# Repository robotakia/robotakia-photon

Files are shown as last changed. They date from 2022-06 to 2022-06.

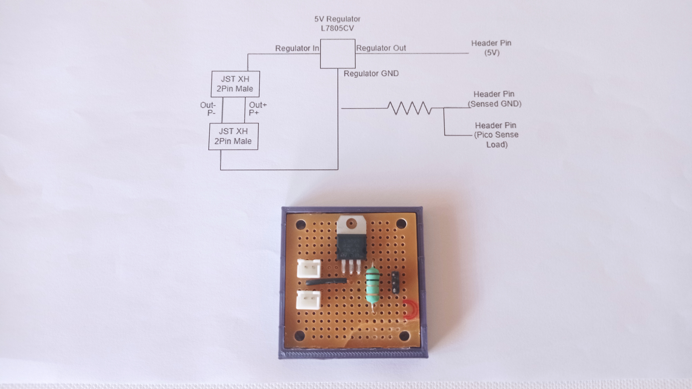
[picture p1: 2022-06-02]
Hardware/Examples/voltage regulator.jpg

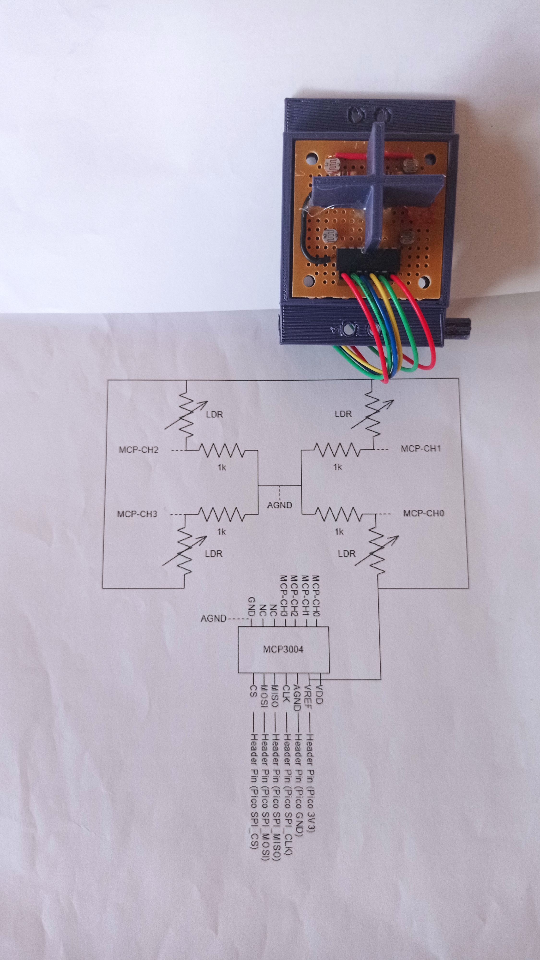
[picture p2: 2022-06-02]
Hardware/Examples/sun tracking sensors.jpg

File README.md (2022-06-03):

# robotakia-photon

Καθώς η ηλεκτρική ενέργεια αποτελεί ένα απαραίτητο αγαθό στον σημερινό τρόπο ζωής μας, σκεφτήκαμε να υλοποιήσουμε ένα σύστημα παραγωγής πράσινης ενέργειας. Η υλοποίηση βασίζεται στην τεχνολογία των φωτοβολταϊκών κυψελών και το σύστημα θα σχεδιαστεί με τρόπο που να μεγιστοποιεί την παραγωγή ενέργειας από τον ήλιο καθ’ όλη τη διάρκεια της μέρας.

-	Η συστοιχία των φωτοβολταϊκών κυψελών θα έχει δύο βαθμούς ελευθερίας, δύο κινητήρες ελέγχουν τον προσανατολισμό του συστήματος
-	Θα υλοποιηθεί πλακέτα/αισθητήρας για αναγνώριση της θέσης του ήλιου, η πλακέτα θα αποτελείται από φωτοαντιστάτες τους οποίους θα «διαβάζει» ο μικροεπεξεργαστής (raspberry pi pico)
-	Το σύστημα θα κάνει αυτόματες διορθώσεις προσανατολισμού πάνω/κάτω και δεξιά/αριστερά για να μεγιστοποιείται η παραγωγή ηλεκτρικής ενέργειας κατά τη διάρκεια της μέρας, ο ιδανικός προσανατολισμός θα προκύπτει από τις τιμές των φωτοαντιστάσεων

Η σελίδα του διαγωνισμού είναι https://openedtech.ellak.gr/robotics2022/sun-tracking-solar-panel-robotakia-photon/

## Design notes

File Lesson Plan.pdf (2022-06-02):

## Περιεχόμενα

## Προετοιμασία

### Λογισμικό

Thonny: Για την συγγραφή του κώδικα Python για το Raspberry Pi Pico.

Tinkercad: Για την σχεδίαση των δομικών στοιχείων.

Prusa Slicer: Για την δημιουργία του gcode για τον 3D εκτυπωτή.

### Εξοπλισμός

Απαραίτητος εξοπλισμός:

- Σταθμός συγκόλλησης
- 3D εκτυπωτής

Βοηθητικός εξοπλισμός:

- Θερμόκολλα

### Υλικά

Quantity | Description
1 | Li-ion Battery Charger Protection Module 2S 3A
1 | Μετατροπέας DC-DC Step-Up 5-35V 2A
2 | Μπαταριοθήκη 1x18650 - με Καλώδια
2 | Μπαταρία Λιθίου 18650 3.7V
1 | Raspberry Pi Pico
2 | Pin Header 1x40 Male 2.54 mm Black
1 | Voltage Regulator L7805CV - 5V 1.5A
2 | Servo Micro 1.8kg.cm Metal Gears (Feetech FS90MG)
4 | Φωτοαντίσταση LDR 5mm
2 | Πλακέτα Διάτρητη 91x45mm (σπάει σε 2 45x45 η κάθε μία)
4 | Αντίσταση Carbon 1/4W 5% 1Kohm
4 | Φωτοβολταϊκή Κυψέλη 1W 125x63mm
7 | JST XH Jumper 2 Wire Assembly - 20cm
7 | JST XH Conector 2-Pin Male 2.5mm
1 | JST XH Jumper 3 Wire Assembly - 20cm
1 | JST XH Conector 3-Pin Male 2.5mm

4 | Schottky Rectifier - 1A 1N5819
1 | PrimaSelect PLA PRO Filament - 1.75mm - 750g spool - Black
2 | Αντίσταση Carbon 2W 5% 1ohm
1 | MCP3004 - 10bit 4 channel ADC SPI
1 | Θερμοσυστελλόμενο 6.4/3.2mm Διάφανο - 1m

## Σενάριο

Καθώς η ηλεκτρική ενέργεια αποτελεί ένα απαραίτητο αγαθό στον σημερινό τρόπο ζωής μας, σκεφτήκαμε να υλοποιήσουμε ένα σύστημα παραγωγής πράσινης ενέργειας. Η υλοποίηση βασίζεται στην τεχνολογία των φωτοβολταϊκών κυψελών και το σύστημα θα σχεδιαστεί με τρόπο που να μεγιστοποιεί την παραγωγή ενέργειας από τον ήλιο καθ’ όλη τη διάρκεια της μέρας.

### Προσέγγιση προβλήματος

Οι φωτοβολταικές κυψέλες παράγουν ηλεκτρική ενέργεια μέσω της ηλιακής ακτινοβολίας και η ισχύς που παράγουν εξαρτάται διάφορους παράγοντες όπως η θέση τους σε σχέση με τον ήλιο, ο καιρός, τα χρόνια λειτουργίας των κυψελών κτλ.

Προφανώς, κάποιους από τους παράγοντες όπως ο καιρός δεν μπορούμε να τους ελέγξουμε. Υπάρχουν όμως κάποιοι παράγοντες τους οποίους μπορούμε να βελτιστοποιήσουμε, για παράδειγμα την κλίση του συστήματός μας ως προς τον ήλιο.

Συνεπώς, η βασική ιδέα για την βελτιστοποίηση της παραγωγής ηλεκτρικής ενέργειας μέσω φωτοβολταϊκών κυψελών είναι η αυτόματη αναπροσαρμογή της κλίσης των κυψελών ως προς τον ήλιο.

### Έρευνα

Ο ήλιος αλλάζει θέση διαρκώς σε σχέση με εμάς. Η τροχιά που βλέπουμε να διαγράφει ο ήλιος σε σχέση με τη γη, η οποία μας είναι ιδιαίτερα οικεία, είναι η κίνηση από την ανατολή προς την δύση κατά τη διάρκεια της μέρας. Αυτό που ίσως να μην έχουμε παρατηρήσει είναι η διαφορετική θέση του ήλιου στον ουράνιο θόλο κατά την αλλαγή των εποχών!

Από παρατήρηση τις θέσης του ήλιου κατά τη διάρκεια της μέρας, συμπεραίνουμε ότι το σύστημα που θα υλοποιήσουμε θα χρειαστεί δύο βαθμούς ελευθερίας. Θα χρειαστεί δηλαδή να μπορεί να βελτιστοποιεί τη θέση των κυψελών ως προς τον ήλιο κατά τη διάρκεια της μέρας ακολουθώντας την πορεία του από ανατολή μέχρι δύση, αλλά θα πρέπει να κάνει και διορθώσεις για την αλλαγή του «ύψους» του ήλιου. Οι διορθώσεις «ύψους» σε σταθερά πάνελ γίνονται μόνο μερικές φορές τον χρόνο, αλλά καθώς το δικό μας σύστημα θα λειτουργεί αυτόματα, οι διορθώσεις θα γίνονται καθ’ όλη τη διάρκεια της μέρας, στοχεύοντας έτσι τον ήλιο ανά πάσα στιγμή.

Το τελικό συμπέρασμα για την υλοποίηση είναι ότι το σύστημα θα πρέπει να μπορεί να κινεί τις κυψέλες δεξιά/αριστερά και πάνω/κάτω.

### Σχεδιασμός συστήματος

Για το σύστημά μας θα επιλέξαμε 4 Φωτοβολταϊκές κυψέλες 1W 125x63mm οι οποίες δίνουν περίπου 6V.

Για το μικροελεγκτή θα χρησιμοποιήσουμε το raspberry pi pico, το οποίο λειτουργεί με τάση 5V για τροφοδοσία και τάση 3.3V στους ακροδέκτες.

Τα θέματα που δημιουργούνται είναι τα εξής:

- Οι μπαταρίες πρέπει να είναι επαναφορτιζόμενες
- Μία μπαταρία δεν δίνει αρκετή τάση για να τροφοδοτεί με 5V τα ηλεκτρονικά μας
- Οι φωτοβολταϊκές κυψέλες δεν δίνουν αρκετή τάση για να φορτίσουν δύο μπαταρίες αν αυτές είναι σε σειρά
- Οι μπαταρίες λιθίου χρειάζονται κύκλωμα προστασίας για την ασφαλή φόρτιση και εκφόρτιση

Επιλέγουμε τα πάνελ να τα συνδέσουμε παράλληλα ώστε να κρατήσουμε την τάση σχετικά χαμηλά και να μεγαλώσουμε το ρεύμα (δύο πάνελ σε σειρά δίνουν διπλάσια τάση, δύο πάνελ παράλληλα δίνουν διπλάσιο ρεύμα σε ιδανικές συνθήκες).

Στην περίπτωση που τα πάνελ δεν παράγουν αρκετή ενέργεια, θέλουμε το σύστημά μας να συνεχίσει να λειτουργεί, συνεπώς θα χρειαστούμε τουλάχιστον δύο μπαταρίες σε σειρά για να δημιουργήσουμε τάση μεγαλύτερη των 5V.

Για να μπορούμε να φορτίσουμε δύο μπαταρίες σε σειρά χρειαζόμαστε μία τάση μεταξύ 8V και 8.4V. Αυτό σημαίνει ότι θα χρειαστεί να βρούμε ένα κατάλληλο σύστημα το οποίο δέχεται μία τάση μικρότερη της ιδανικής (η τάση από τα πάνελ) και την μετατρέπει στην μεγαλύτερη ιδανική (η τάση που φορτίζουν οι μπαταρίες). Τέτοια συστήματα ονομάζονται Boost Converters. Η έξοδος του συστήματος αυτού θέλουμε να είναι μεταξύ 8V και 8.4V.

Το τελευταίο θέμα που χρειάζεται να λύσουμε είναι η τάση τροφοδοσίας για τον ελεγκτή μας, η οποία πρέπει να είναι 5V. Για τον σκοπό αυτό θα βρούμε ένα σύστημα το οποίο παίρνει μία τάση μεγαλύτερη από την απαιτούμενη (για εμάς θα δέχεται γύρω στα 8V) και θα την υποβιβάζει σε σταθερά 5V. Αυτά τα συστήματα λέγονται voltage regulators.

Στο σύστημά μας θα χρησιμοποιήσουμε δύο κινητήρες servo για τους δύο βαθμούς ελευθερίας (καθώς είναι αρκετά εύχρηστοι και οικονομικοί) και 4 LDR (light dependent resistor) για την αναγνώριση της θέσης του ήλιου.

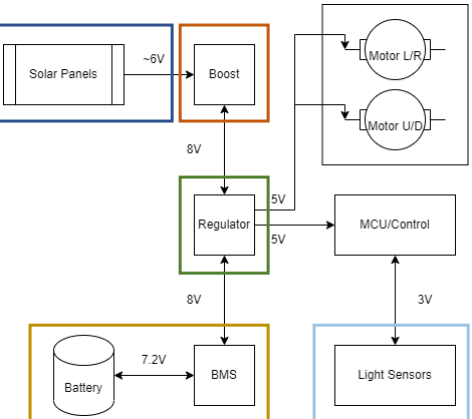
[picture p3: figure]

Επιλογή βασικών στοιχείων
Φωτοβολταϊκή Κυψέλη 1W 125x63mm

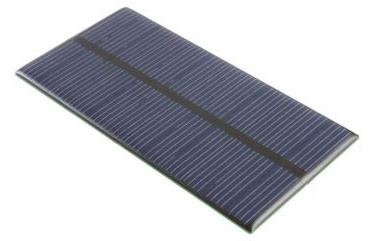
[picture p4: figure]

Μετατροπέας DC-DC Step-Up 5-35V 2A (boost converter)

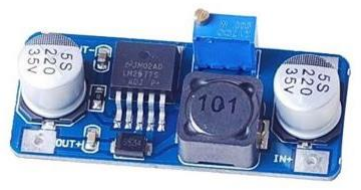
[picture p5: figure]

Li-ion Battery Charger Protection Module 2S 3A

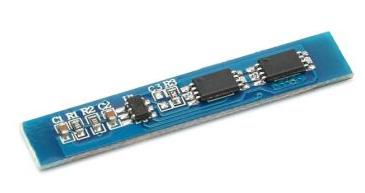
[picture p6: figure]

Voltage Regulator L7805CV - 5V 1.5A

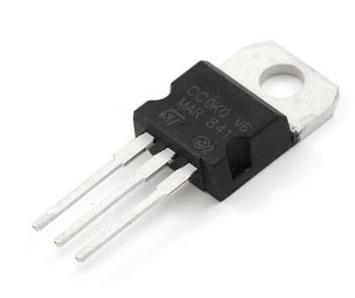
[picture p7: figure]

Servo Micro 1.8kg.cm Metal Gears (Feetech FS90MG)

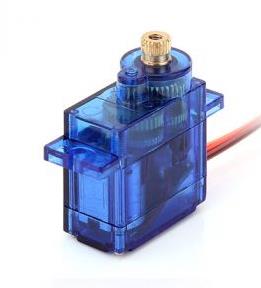
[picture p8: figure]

Μπαταρία Λιθίου 18650 3.6V 3200mAh - LG INR18650-MH1

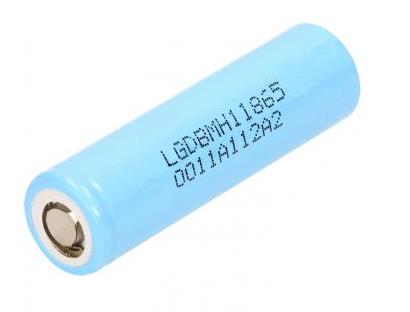
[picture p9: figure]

Σχεδιασμός υλικού
Πάνελ

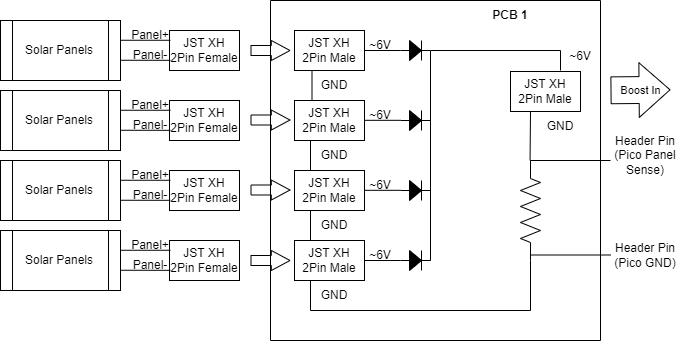
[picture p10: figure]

Ανύψωση τάσης (Boost DC/DC)

Μπαταρίες

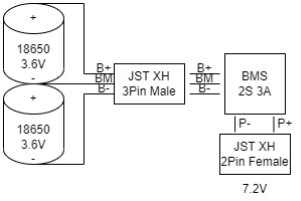
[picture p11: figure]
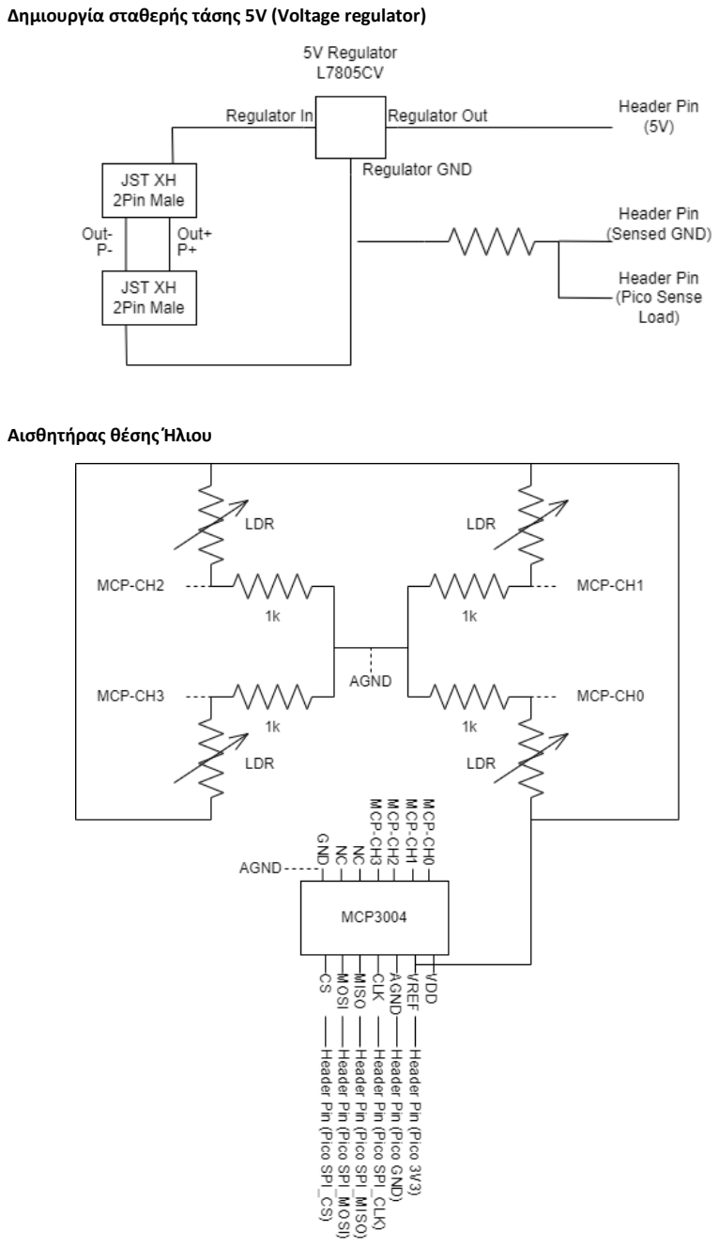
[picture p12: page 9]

Δημιουργία σταθερής τάσης 5V (Voltage regulator)

Αισθητήρας θέσης Ήλιου

Σχεδιασμός δομικών στοιχείων

Βάση

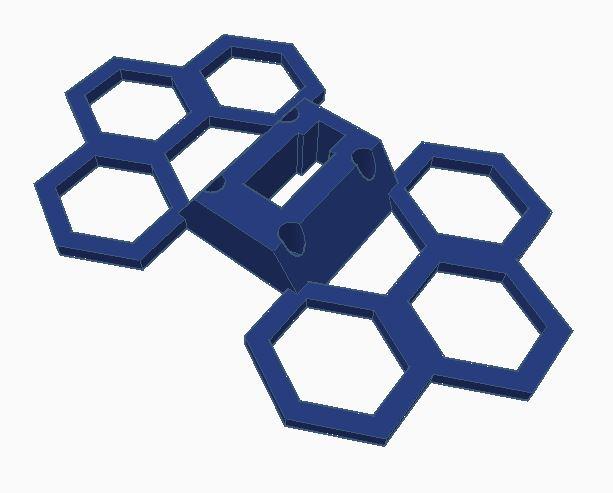
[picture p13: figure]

Η βάση σχεδιάζεται ώστε να παρέχει επαρκή στατικότητα στο σύστημά μας. Στο κέντρο της βάσης δημιουργούμε οπή στις διαστάσεις του κινητήρα servo.

Σύνδεσμος servo βάσης

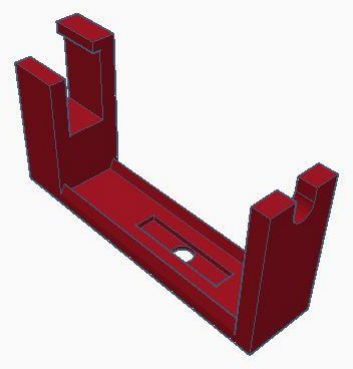
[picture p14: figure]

Ο σύνδεσμος βάσης τοποθετείται πάνω στον κινητήρα βάσης και επιτρέπει να περιστροφή των πάνελ δεξιά και αριστερά. Στη μία μεριά υπάρχει εσοχή για τον δεύτερο κινητήρα servo και από την άλλη έχει σχεδιαστεί εγκοπή για να μπορεί να υπάρχει υποστήριξη των πάνελ και να στέκονται ίσια.

Σύνδεσμος πάνελ

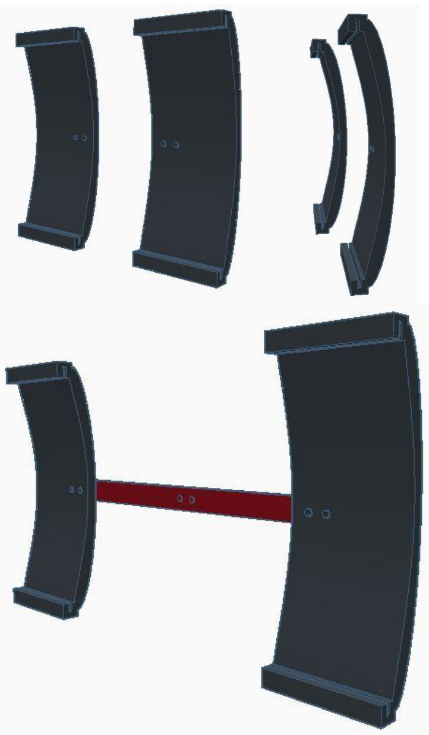
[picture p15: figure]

Τα πάνελ εφαρμόζουν συρταρωτά, δύο σε κάθε βάση πάνελ, και οι δύο αυτές βάσης βιδώνονται πάνω στον άξονα στήριξης.

Σύνδεσμος servo κλίσης

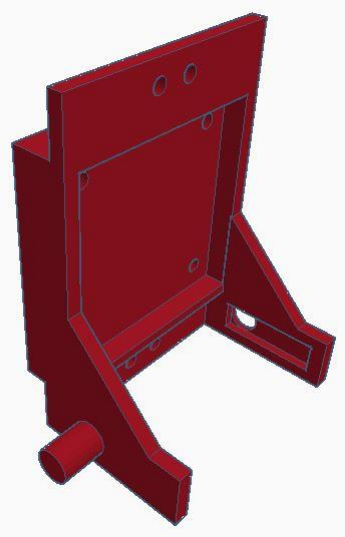
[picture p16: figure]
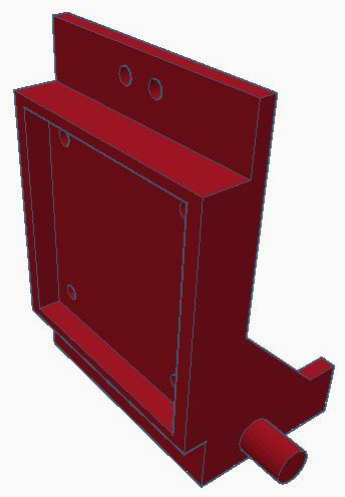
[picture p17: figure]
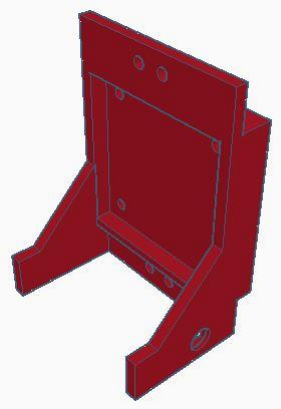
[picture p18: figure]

Στο κεντρικό εξάρτημα θα βιδωθεί ο άξονας με τις βάσεις των πάνελ (και τα ίδια τα πάνελ) στις δύο κάτω οπές. Στο αρχικό σχέδιο βιδώνονταν στις πάνω, αλλά το κέντρο βάρους του συστήματος ήταν μακριά από τον άξονα περιστροφής, με αποτέλεσμα να χρειάζεται περισσότερη ενέργεια για να μετακινείται το σύστημα.

Ο κύλινδρος στο κάτω μέρος της μίας μεριάς παρέχει υποστήριξη του βάρους των πάνελ. Στην άλλη μεριά βλέπουμε την εσοχή για τον άξονα του κινητήρα που επιτρέπει να αλλαγή της κλίσης του συστήματος.

Στην μπροστά τετράγωνη εσοχή, τοποθετείται η πλακέτα με τους αισθητήρες φωτός και στην πίσω η πλακέτα στην οποία συνδέονται τα πάνελ.

Υλοποίηση υλικού
Το υλικό μπορεί να υλοποιηθεί σε διάτρητες πλακέτες, το οποίο αν και είναι πιο δύσκολο στην υλοποίηση προτείνεται λόγω της σθεναρότητας που θα έχει έτσι το σύστημα. Διαφορετικά, όλες οι συνδεσμολογίες γίνεται σε breadboard, το οποίο είναι πιο εύκολο να υλοποιηθεί, αλλά συνήθως πολλά καλώδια χρειάζονται επανασύνδεση λόγω της έλλειψης κολλήσεων.

Μπαταρίες και BMS

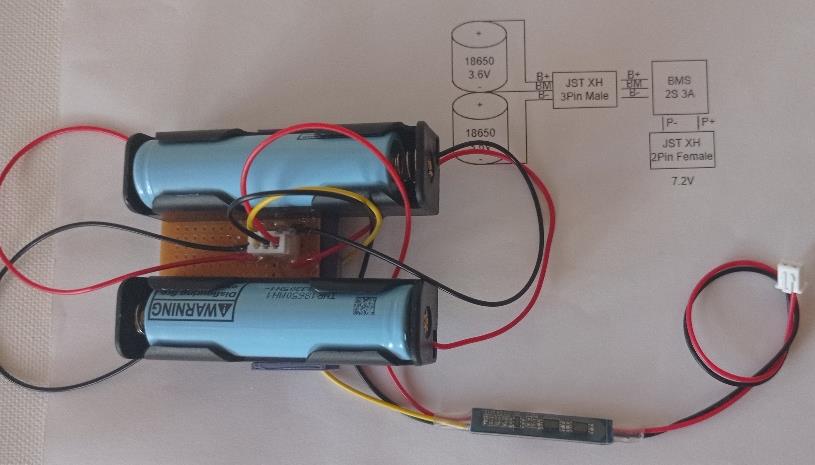
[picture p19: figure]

Ανύψωση τάσης (Boost DC/DC)

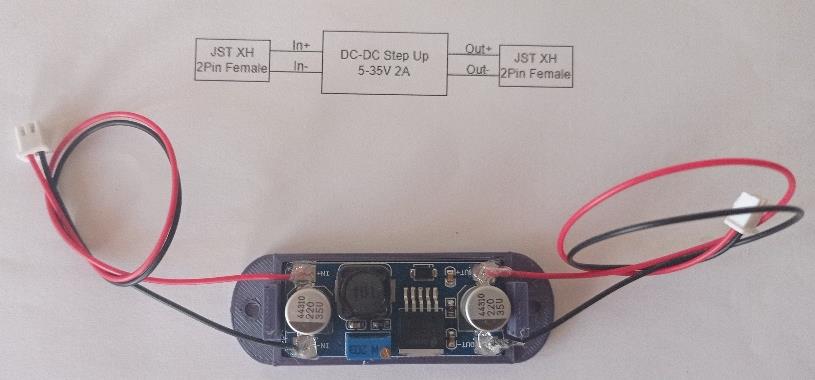
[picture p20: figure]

Συλλέκτης Πάνελ

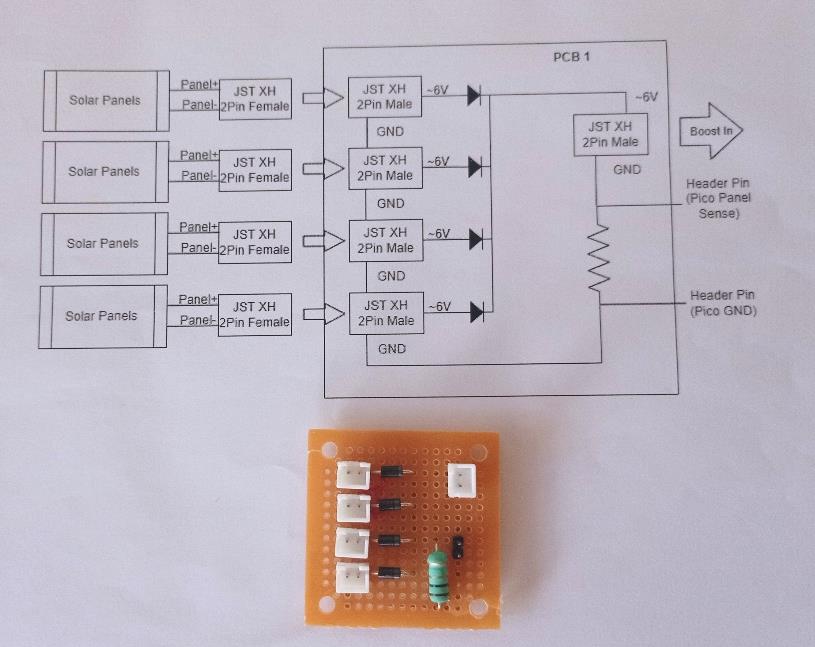
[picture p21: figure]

Αισθητήρας θέσης Ήλιου

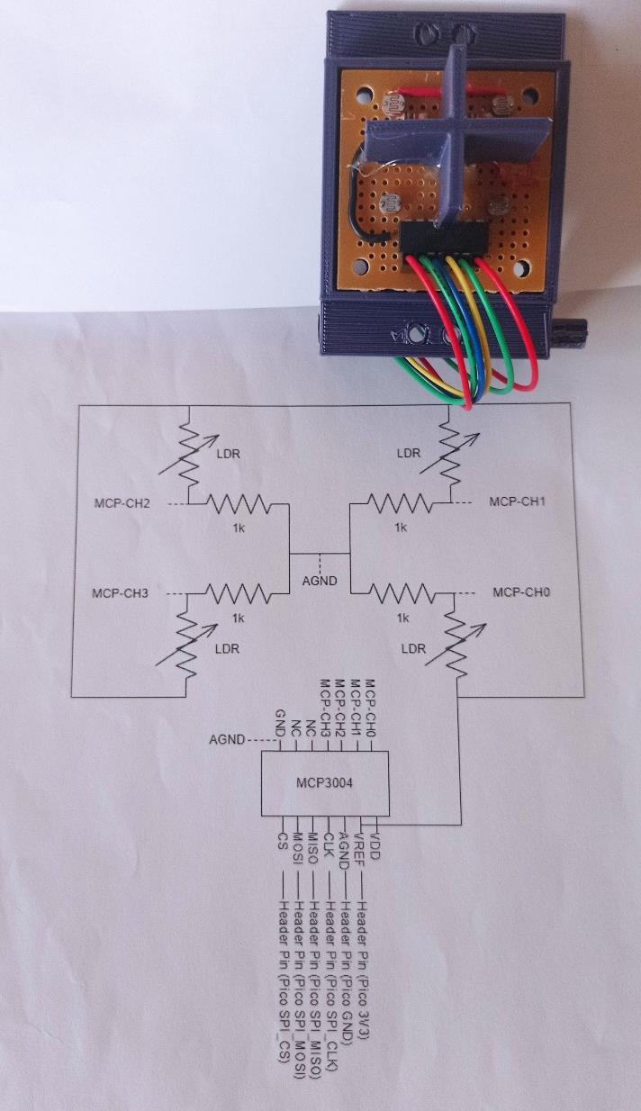
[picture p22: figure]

Δημιουργία σταθερής τάσης 5V (Voltage regulator)

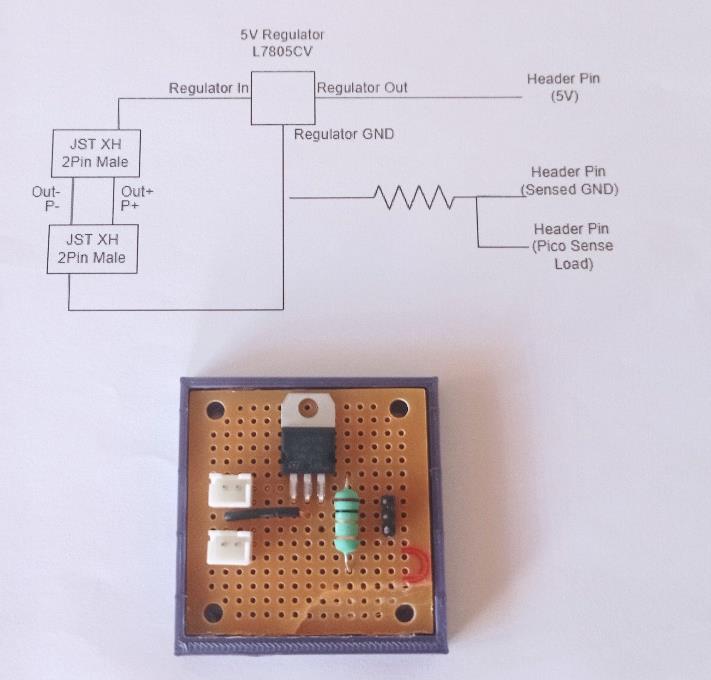
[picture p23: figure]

Σχεδιασμός λογισμικού
Σημείωση: Για τη λειτουργία του προγράμματος χρησιμοποιείται η βιβλιοθήκη mcp3004. Για να έχουμε πρόσβαση σε αυτή, θα πρέπει το αρχείο mcp3004.py να περαστεί στη μνήμη flash του Raspberry Pi Pico.

Φόρτωση βιβλιοθηκών.

from time import *
from machine import *
from mcp3004 import MCP3004

Αρχικοποίηση ακροδεκτών για το SPI. """ SPI Parameters """
SPI_CLK = Pin(2)
SPI_MOSI = Pin(3)
SPI_MISO = Pin(4)
SPI_CS = Pin(5, Pin.OUT)

Αρχικοποίηση SPI και βιβλιοθήκης του ολοκληρωμένου MCP3004.
spi = SPI(0, sck=SPI_CLK, mosi=SPI_MOSI, miso=SPI_MISO, baudrate=100000) cs = SPI_CS

mcp = MCP3004(spi, cs)

Αρχικοποίηση ακροδεκτών για αναλογική ανάγνωση.
""" ADC Parameters """
SPANEL_PIN = Pin(26, Pin.IN) # Sense PANEL PIN
SPOUT_PIN = Pin(27, Pin.IN) # Not Used! Sense Power OUT PIN

sPanel = ADC(SPANEL_PIN)
sPout = ADC(SPOUT_PIN)

Αρχικοποίηση ακροδεκτών σε PWM 50Hz για έλεγχο της θέσης των κινητήρων servo. """ Control Parameters """
SERVO_LR_PIN = Pin(15, Pin.OUT)
SERVO_UD_PIN = Pin(14, Pin.OUT)

servoLR = PWM(SERVO_LR_PIN) servoUD = PWM(SERVO_UD_PIN) servoLR.freq(50) # 50Hz
servoUD.freq(50) # 50Hz

Αρχικοποίηση λοιπών παραμέτρων συστήματος. """ System Parameters """
onboardLED = Pin(25, Pin.OUT)

SYS_ADC_ACCURACY = 0xFFFF # system ADC is 16 bit MCP_ADC_ACCURACY = 0xFFF # mcp ADC is 12 bit

Πλήθος αισθητήρων φωτός.
NUM_LDR = 4 # number of Light Dependent Resistors in our system

Το σύστημά μας λειτουργεί στα 3.3V. Η τάση αναφοράς χρειάζεται για να μετατρέψουμε τιμή βήματος του ADC σε τιμή τάσης σε mV.
SYS_mV_REF = 3300 # system votlage reference in mV
Η τιμή της αντίστασης μέτρησης ρεύματος χρειάζεται για να μετατρέψουμε την αναλογική τάση σε τιμή ρεύματος σε mA.
SENSE_RES_VALUE = 1 # value of sensing resistors

Ο χρόνος που το σύστημα θα πέσει σε καταστολή μέχρι να χρειαστεί να πάρει νέα μέτρηση. SLEEP_TIME = 2000 # changes if isDemo is not 0

Η διαφορά που χρειάζεται να έχουν οι αισθητήρες μεταξύ τους ώστε το σύστημα να διορθώσει την θέση του ως προς τον ήλιο.
SENSITIVITY = 3
Η μοίρες που μετακινεί τον αντίστοιχο κινητήρα για κάθε διόρθωση.
SERVO_STEP = 1

Αντιστοίχιση καναλιών MCP σε θέση αισθητήρα.
# sensor-mcp channel mapping

LDR_UR = 1 # up right ldr when looking from the front LDR_UL = 2 # up left ldr when looking from the front LDR_DR = 0 # down right ldr when looking from the front LDR_DL = 3 # down left ldr when looking from the front

Ακραίες τιμές κινητήρων για δεξιά-αριστερά, πάνω-κάτω. LR_MIN = 30
LR_MAX = 150
UD_MIN = 90
UD_MAX = 150

""" ======================
=== System and functions ===
========================= """
Υπολογίζει τη σχέση μεταξύ των διαφορετικών αισθητήρων για δεδομένη ένταση φωτός. Για να γίνει σωστά ο υπολογισμός θα πρέπει, όταν κληθεί αυτή η συνάρτηση, οι αισθητήρες να είναι εκτεθειμένοι στην ίδια ένταση φωτός.
def CalcSensorNormalization():
acc_ldr = [0, 0, 0, 0]

for i in range(10):
sensorValues = ReadLightSensors_raw()

for j in range(NUM_LDR):
acc_ldr[j] += sensorValues[j] sleep_ms(100)

for i in range(NUM_LDR):
print(acc_ldr[i], end=' ') print()

normValues = [1., 1., 1., 1.]
for i in range(NUM_LDR):
normValues[i] = round(sensorValues[0] / sensorValues[i], 2) print(normValues[i], end=" ")
print()

Διαβάζει την αναλογική τάση από τον ADC που δίνεται σαν όρισμα και τη μετατρέπει σε τιμή ρεύματος σε mA.
def ReadCurrent(sourceADC):
rawValue = sourceADC.read_u16()
voltage = rawValue * SYS_mV_REF / SYS_ADC_ACCURACY current = voltage / SENSE_RES_VALUE # I = V/R (R=1 in our case)

return round(current) # return current in mA

""" ================================
=== Energy production monitoring === ==================================== """
Υπολογίζει την παραγόμενη ισχύ βάση του μετρούμενου παραγόμενου ρεύματος. def UpdateEnergyValues():
global panelCurrent, panelWatt

panelCurrent = (panelCurrent + ReadCurrent(sPanel)) >> 1 # division by shifting panelWatt = pow(panelCurrent, 2) * SENSE_RES_VALUE / 1000 # divide by 1000 because of mA ^ 2
panelWatt = round(panelWatt)

Υπολογίζει την συνολική ενέργεια που έχει παράξει το σύστημα όσο λειτουργεί. def CalcPowerProduction():
global productionWatt, productionTime, productionWSeconds

productionWatt += panelWatt # in mW
productionTime += SLEEP_TIME # in ms
productionWSeconds = round(productionWatt * (productionTime/1000) / 3600,
2) # power production in mWHours

""" ================

=== Read sensors ===
==================== """
Διαβάζει τις τιμές των αισθητήρων από το MCP. def ReadLightSensors_raw():
data = []

for i in range(NUM_LDR):
data.append(mcp.read(i))

return data

Διαβάζει τις τιμές των αισθητήρων από το MCP και τις κανονικοποιεί με βάση τη λίστα κανονικοποίησης.
def ReadLightSensors():
global normValues

data = []

for i in range(NUM_LDR):
data.append(round(mcp.read(i) * normValues[i] * 100 / MCP_ADC_ACCURACY, 1))

return data

""" =========================== === Correct system position === =============================== """ Περιορίζει την τιμή value στο όριο low-high.
def ConstraintValues(value, low, high): if value > high:
return high
elif value < low:
return low
else:
return value

Ελέγχει τον κινητήρα servo για να πάει σε συγκεκριμένη γωνία. def ServoDegrees(myServo, angle):
if angle > 180:
angle = 180
elif angle < 0:
angle = 0

duty = (angle / 180) * 6881.175 + 1310.7 myServo.duty_u16(int(duty))

Ελέγχει και τους δύο κινητήρες.

def SetServos(angleUD, angleLR): ServoDegrees(servoUD, angleUD) ServoDegrees(servoLR, angleLR)

Επιστρέφει την τιμή διόρθωσης του συστήματος για το πάνω-κάτω. Η τιμή αυτή εξαρτάται από τις τιμές των αισθητήρων και την ευαισθησία του συστήματος.
def CalcServoUD(ldrUR, ldrUL, ldrDR, ldrDL):
if ldrUR > ldrDR + SENSITIVITY or ldrUL > ldrDL + SENSITIVITY: return -SERVO_STEP
elif ldrUR < ldrDR - SENSITIVITY or ldrUL < ldrDL - SENSITIVITY: return SERVO_STEP
else:
return 0

Επιστρέφει την τιμή διόρθωσης του συστήματος για το δεξιά-αριστερά. Η τιμή αυτή εξαρτάται από τις τιμές των αισθητήρων και την ευαισθησία του συστήματος.
def CalcServoLR(ldrUR, ldrUL, ldrDR, ldrDL):
if ldrUR > ldrUL + SENSITIVITY or ldrDR > ldrDL + SENSITIVITY: return SERVO_STEP
elif ldrUR < ldrUL - SENSITIVITY or ldrDR < ldrDL - SENSITIVITY: return -SERVO_STEP
else:
return 0

""" ===========
=== Display ===
=============== """
Εκτυπώνει στην οθόνη μας χρήσιμες τιμές για παρακολούθηση. def PrintValues():
print("\nCurrent //", end='\t')
print("Panel: " + str(panelCurrent) + " mA", end='\n')

print("Power //", end='\t')
print("Panel: " + str(panelWatt) + " mW", end='\n')

for i in range(len(sensorValues)):
print("LDR" + str(i) + ": " + str(sensorValues[i]), end='\t') print()

print("UD: " + str(angleUD) + "\tLR: " + str(angleLR))

""" ============================
=== Delay and low power mode === ================================ """

Ανάβει για ελάχιστο χρόνο το led που βρίσκεται στο Pico, ώστε να ξέρουμε ότι έγινε λήψη νέας μέτρησης και μετά μπαίνει σε κατάσταση χαμηλής κατανάλωσης μέχρι να περάσει ο υπόλοιπος χρόνος αναμονής.
def BlinkAndWait():
onboardLED.on()
sleep_ms(50) # wait for pulses to be sent to the servos

onboardLED.off()
lightsleep(SLEEP_TIME - 50) # enter low power state and keeping RAM

""" ==========
Main
========== """
ldrUR = 0
ldrUL = 0
ldrDR = 0
ldrDL = 0

angleLR = 90 # set in the middle
angleUD = 135 # set at 45 degrees from being parallel from the ground

panelCurrent = 0
productionWatt = 0
productionTime = 0

Εάν το isDemo είναι 1, τότε το σύστημα τρέχει με τις τιμές παρουσίασης οι οποίες έχουν οριστεί με κατάλληλο τρόπο ώστε το σύστημα να λειτουργεί σε χαμηλότερες τιμές φωτεινότητας (εσωτερικός χώρος) και να περιμένει λιγότερο μεταξύ των μετρήσεων.
# === Select "Is Demo" mode and values ===

isDemo = 1 # set to 0 for normal mode, set to 1 for demo mode
if not isDemo:
normValues = [1.0, 1.05, 1.01, 1.01] # measured on direct sunlight sensorThreshold = 17
else:
normValues = [1.0, 1.54, 1.1, 1.1] # measured indoors sensorThreshold = 7
SLEEP_TIME = 500

# === System init ===

SetServos(angleUD, angleLR)

Βγάζουμε το σχόλιο όταν θέλουμε να βλέπουμε συνέχεια τις τιμές κανονικοποίησης που υπολογίζει το σύστημά μας. Το σύστημα δεν βρίσκεται σε κανονική λειτουργία αν βγάλω τα σχόλια από εδώ.
# while True: # Loop normalization calculation for debugging

# CalcSensorNormalization() # Loop normalization calculation for debugging

CalcSensorNormalization()

while True:
# === Energy production monitoring === UpdateEnergyValues()

CalcPowerProduction()

# === Read sensors ===

Διαβάζουμε τις νέες τιμές αισθητήρων.
sensorValues = ReadLightSensors()

Φιλτράρουμε λίγο τις τιμές από θόρυβο βάζοντας μία μικρή αδράνεια στην αλλαγή τους. ldrUR = (ldrUR + sensorValues[LDR_UR]) / 2 ldrUL = (ldrUL + sensorValues[LDR_UL]) / 2 ldrDR = (ldrDR + sensorValues[LDR_DR]) / 2 ldrDL = (ldrDL + sensorValues[LDR_DL]) / 2

Αν οι τιμές αισθητήρων είναι αρκετά μεγάλες ώστε να θεωρούνται αποδεκτές, τότε υπολογίζονται οι διορθώσεις για τους δύο άξονες.
# === Correct system position ===

if max(sensorValues) > sensorThreshold:
angleUD += CalcServoUD(ldrUR, ldrUL, ldrDR, ldrDL) angleUD = ConstraintValues(angleUD, UD_MIN, UD_MAX)

angleLR += CalcServoLR(ldrUR, ldrUL, ldrDR, ldrDL) angleLR = ConstraintValues(angleLR, LR_MIN, LR_MAX)

SetServos(angleUD, angleLR)

# === Display and save === PrintValues()

# === Delay and low power mode === BlinkAndWait()

### Υλοποίηση τελικού συστήματος

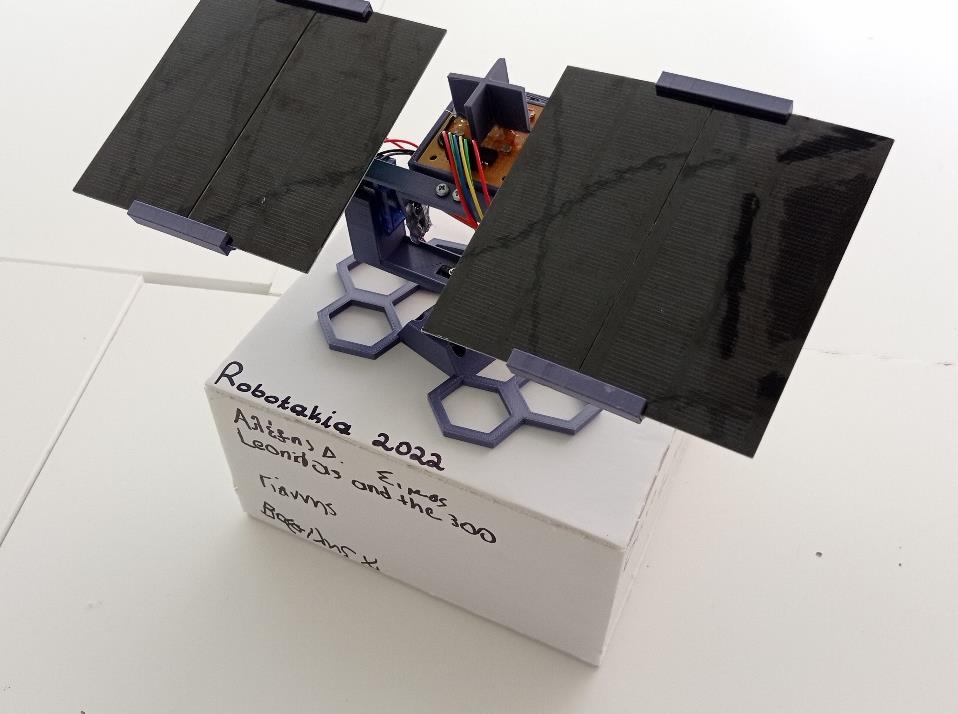
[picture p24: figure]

Τοποθετούμε την βάση σε σταθερό σημείο είτε με κάποια κόλλα, είτε βιδώνοντάς την στις οπές που έχει πάνω σε κάποια μακέτα, κομμάτι ξύλο κτλ.

Τρέχουμε την εντολή SetServos() για τις αρχικές γωνίες σε μία επανάλληψη.

while True:
SetServos(angleUD, angleLR)

Έτσι είμαστε βέβαιοι ότι έχουμε αρχικοποιήσει τους κινητήρες προτού τους κολλήσουμε ή βιδώσουμε πάνω στο σύστημα.

Αφού έχουμε αρχικοποιήσει τους κινητήρες στις επιθυμητές αρχικές θέσεις, κολλάμε ή βιδώνουμε τα αξεσουάρ των κινητήρων στις αντίστοιχες εγκοπές του συνδέσμου servo κλίσης και συνδέσμου servo βάσης.

Στο επόμενο βήμα προετοιμάζουμε τα πάνελ.

Βιδώνουμε πρώτα τον άξονα των πάνελ στις βάσεις τους και προσθέτουμε τα πάνελ. Στη συνέχεια το βιδώνουμε στη βάση των αισθητήρων ή οποία μετά τοποθετείται μαζί με τον άξονα του servo στο σύστημα της βάσης που ετοιμάσαμε προηγουμένως.

Τέλος πραγματοποιούμε όλες τις συνδέσεις καλωδίων με προσοχή για να αποφύγουμε ζημιές και λάθη στη λειτουργία του συστήματος.

Συνδέσεις

Module | Module Pin Name

Pico Pin
Name | Other Connection | Description

Light Sensor PCB

Pico 3v3 | 3V3 (OUT) | Power
Pico GND | GND | Power
Pico SPI_CLK | GP2 | SPI 0
Pico SPI_MISO | GP4 | SPI 0
Pico SPI_MOSI | GP3 | SPI 0
Pico SPI_CS | GP5 | SPI 0

Regulator PCB

Out + | Out + (DC-DC) | Power
Out - | Out - (DC-DC) | Power
P + | P + (BMS) | Power
P - | P - (BMS) | Power
5V | VBUS | Power
Sensed GND | No Connect | User Ground
Pico Sense Load | GP27 | ADC

BMS

P + | P + (Regulator PCB) | Power
P - | P - (Regulator PCB) | Power
B + | LiPo 7.2V | Power
BM | LiPo 3.6V
B - | LiPo GND | Power

DC-DC Step Up

In + | ~6V (Panel) | Power
In - | GND (Panel) | Power
Out + | Out + (Regulator
| PCB) | Power
Out - | Out - (Regulator PCB) Power

Panel

~6V | In + (DC-DC) | Power
GND | In - (DC-DC) | Power
Pico Panel Sense | GP26 | ADC
Pico GND | GND | Power
Servo Up-Down | GP14 | PWM
Servo Left-Right | GP15 | PWM

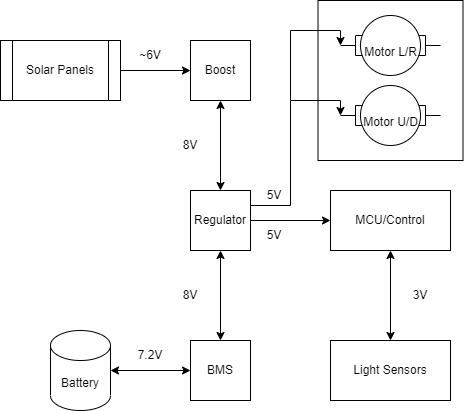
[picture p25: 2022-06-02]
Hardware/SystemArchitecture.png

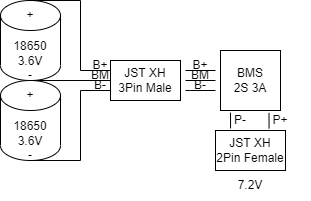
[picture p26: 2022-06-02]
Hardware/BatteryProtection.png

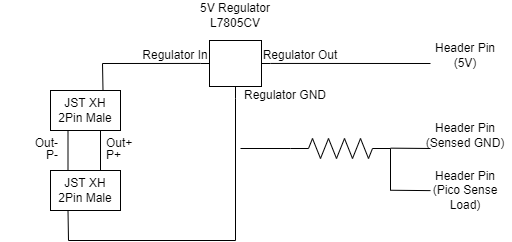
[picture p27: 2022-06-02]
Hardware/Regulator.png

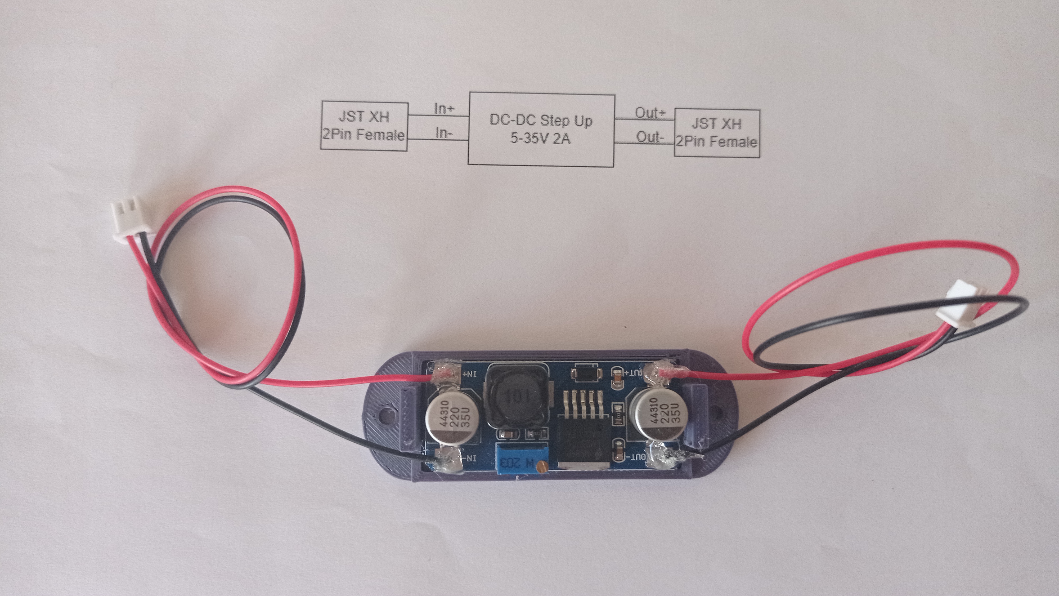
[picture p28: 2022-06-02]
Hardware/Examples/boost DC-DC.jpg

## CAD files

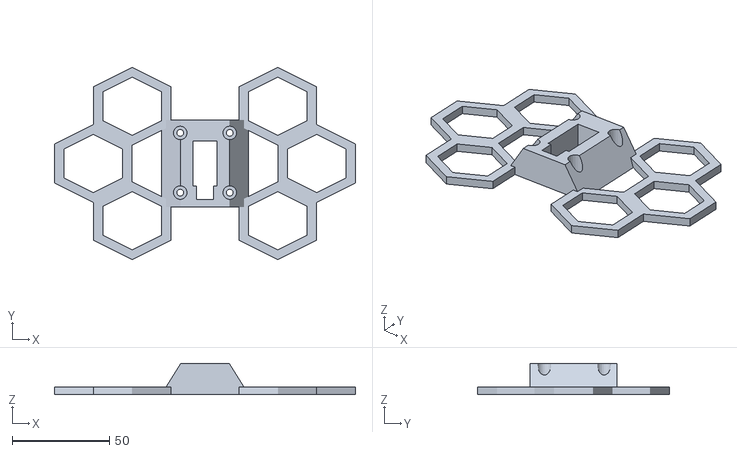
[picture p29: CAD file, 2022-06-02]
3D Printing/System Base - Sun tracking solar panel.stl
155.0 x 99.0 x 16.0

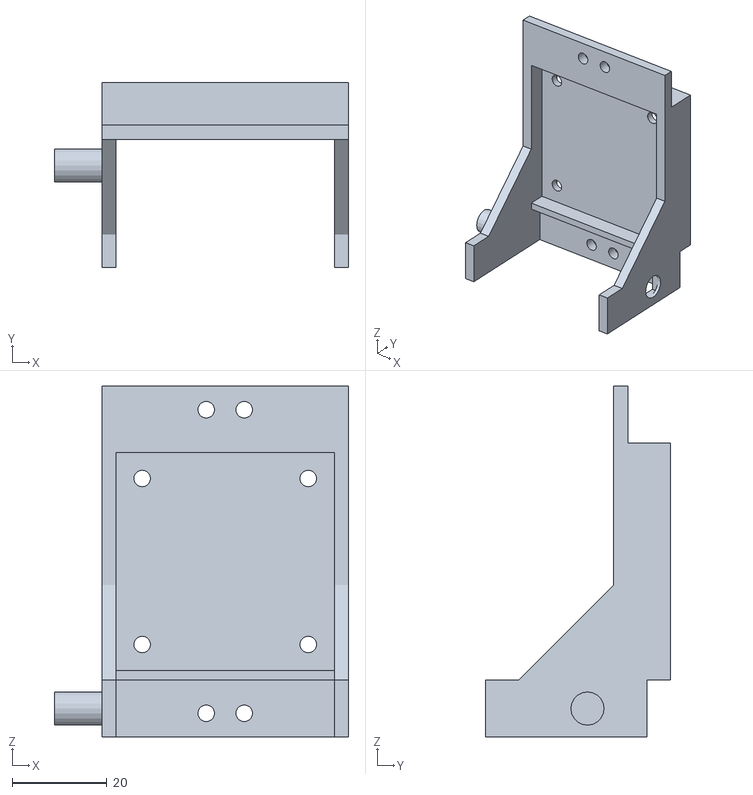
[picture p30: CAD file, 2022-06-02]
3D Printing/Sensor Mount - Sun tracking solar panel.stl
62.0 x 39.0 x 74.0

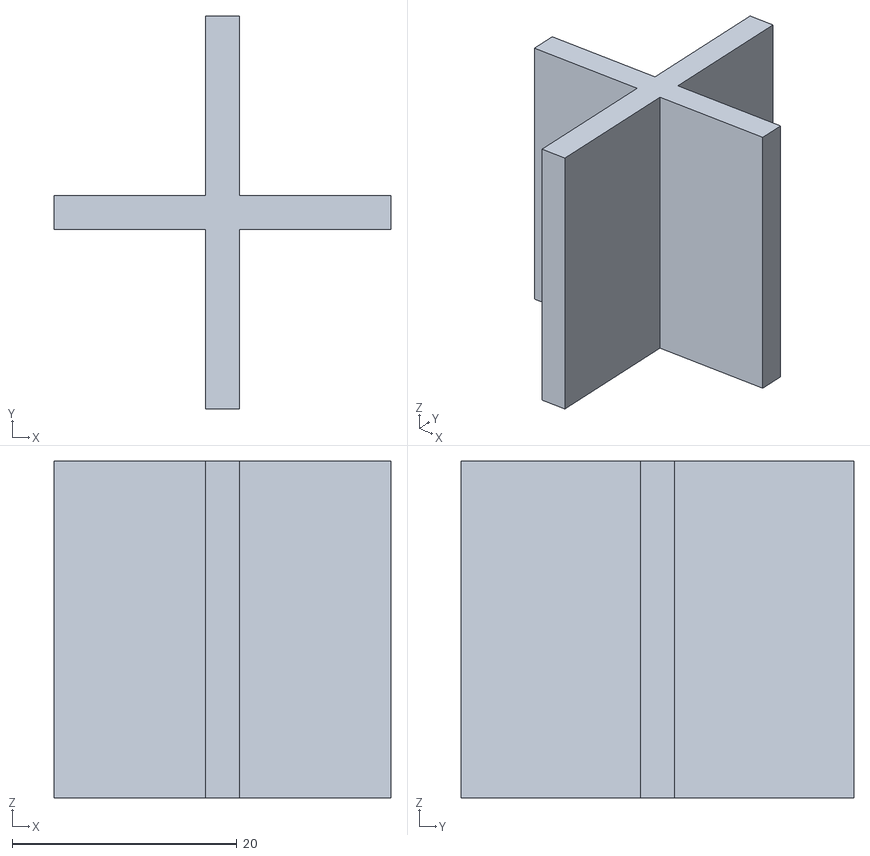
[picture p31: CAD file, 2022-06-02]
3D Printing/Shader - Sun tracking solar panel.stl
30.0 x 35.0 x 30.0

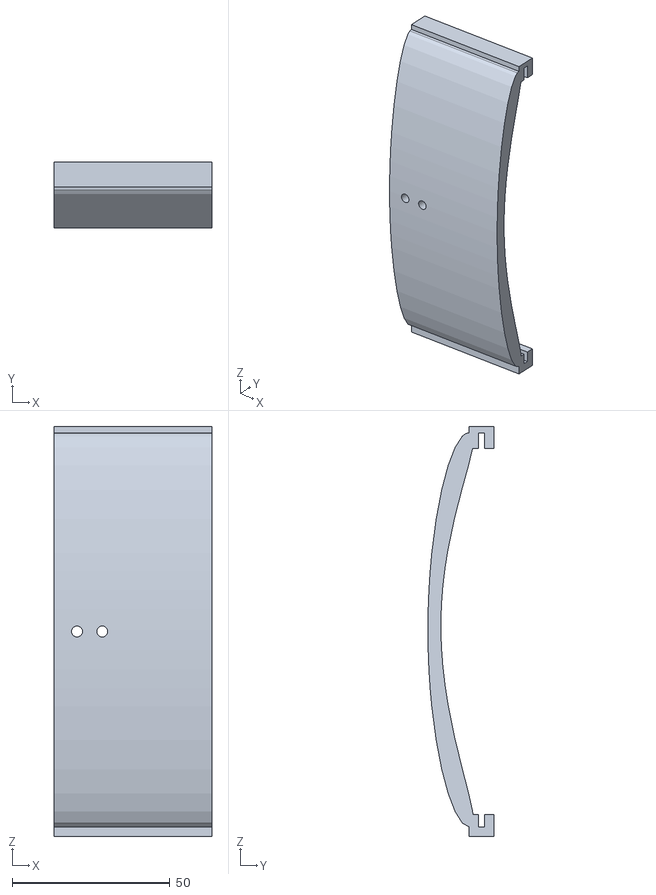
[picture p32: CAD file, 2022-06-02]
3D Printing/Panel Mount - Sun tracking solar panel.stl
50.0 x 21.0 x 130.0

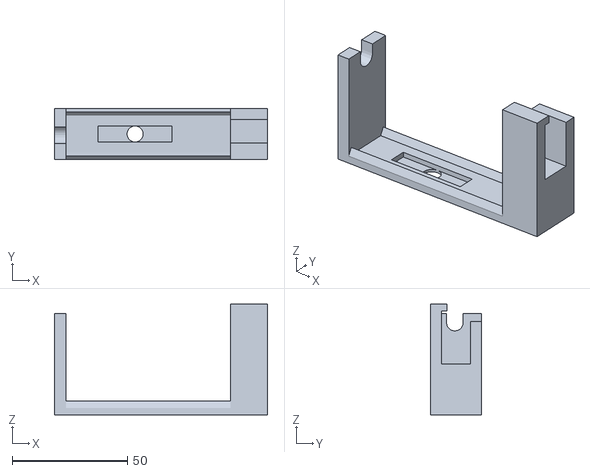
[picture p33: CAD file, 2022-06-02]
3D Printing/Servo Mount - Sun tracking solar panel.stl
92.5 x 22.0 x 48.0

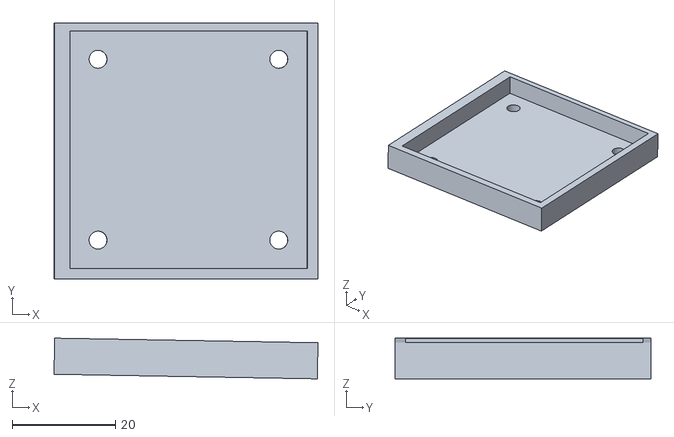
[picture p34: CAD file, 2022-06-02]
3D Printing/Regulator - Sun tracking solar panel.stl
51.1 x 49.5 x 7.89

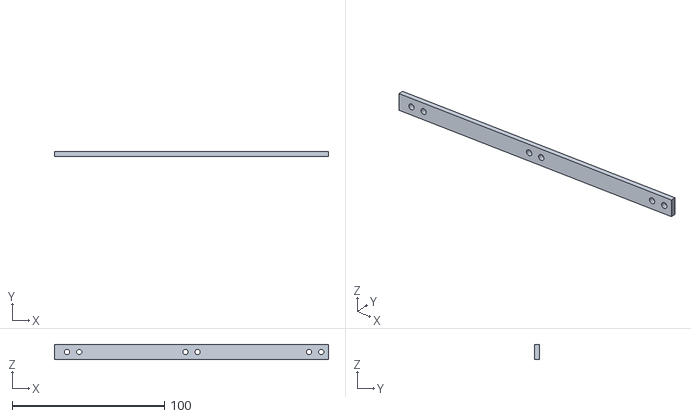
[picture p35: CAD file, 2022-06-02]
3D Printing/Mounting Bar - Sun tracking solar panel.stl
180.0 x 3.00 x 10.0

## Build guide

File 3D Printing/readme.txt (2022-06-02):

Τα STL αρχεία αποτελούν τα τρισδιάστατα μοντέλα των δομικών στοιχείων του συστήματος.

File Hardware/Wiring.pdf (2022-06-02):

Module | Module Pin Name | Pico Pin Name Other Connection | Description
| Pico 3v3 | 3V3 (OUT) | Power
| Pico GND | GND | Power
| Pico SPI_CLK | GP2 | SPI 0
| Pico SPI_MISO | GP4 | SPI 0
| Pico SPI_MOSI | GP3 | SPI 0
| Pico SPI_CS | GP5 | SPI 0
| Out + | Out + (DC-DC) | Power
| Out - | Out - (DC-DC) | Power
| P + | P + (BMS) | Power
| P - | P - (BMS) | Power
| 5V | VBUS | Power
| Sensed GND | User Ground
| Pico Sense Load | GP27 | ADC
| P + | P + (Regulator PCB) | Power
| P - | P - (Regulator PCB) | Power
| B + | LiPo 7.2V | Power
| BM | LiPo 3.6V
| B - | LiPo GND | Power
| In + | ~6V (Panel) | Power
| In - | GND (Panel) | Power
| Out + | Out + (Regulator PCB) | Power
| Out - | Out - (Regulator PCB) | Power
| ~6V | In + (DC-DC) | Power
| GND | In - (DC-DC) | Power
| Pico Panel Sense | GP26 | ADC
| Pico GND | GND | Power
Servo Up-Down | | GP14 | PWM
Servo Left-Right | | GP15 | PWM

Light Sensor PCB

Regulator PCB

BMS

DC-DC Step Up

Panel
